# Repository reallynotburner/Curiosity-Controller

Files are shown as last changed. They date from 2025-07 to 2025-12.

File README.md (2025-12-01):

# Curiosity-Rover

<p style="text-align: center;">
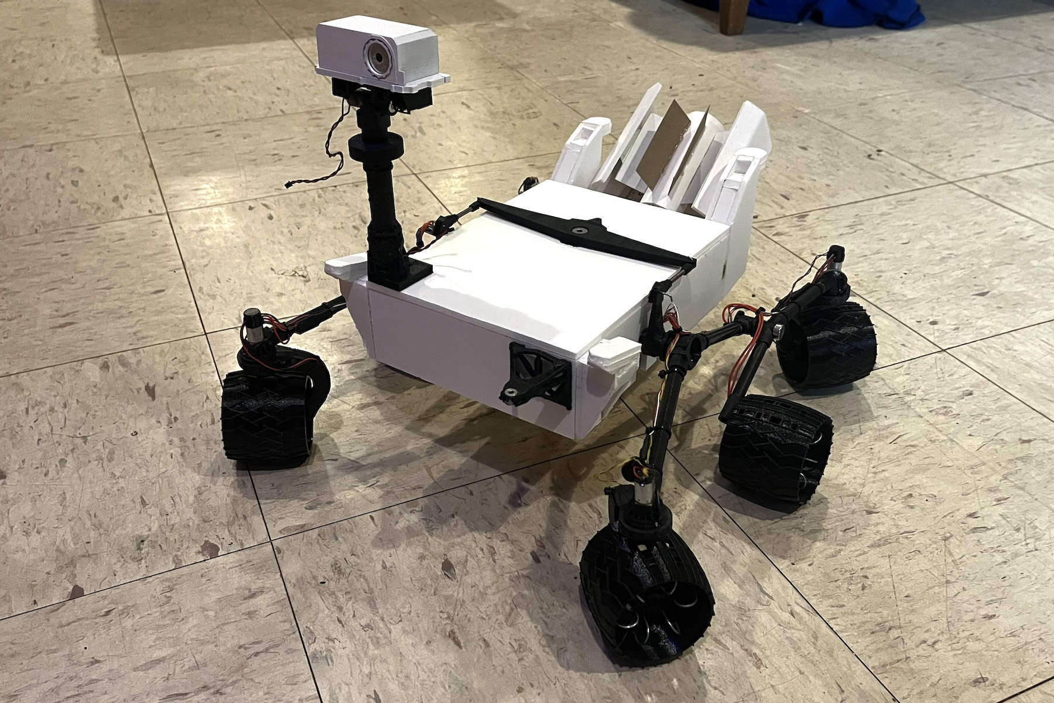
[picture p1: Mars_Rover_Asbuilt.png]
    
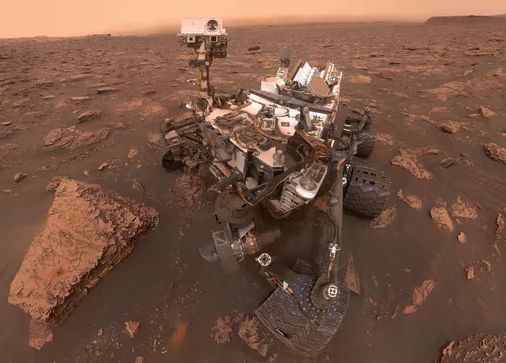
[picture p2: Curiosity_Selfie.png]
    
</p>

## Goal
###
I want to drive around a highly functional model of the Mars Science Laboratory (MSL), named [Curiosity](https://www.jpl.nasa.gov/missions/mars-science-laboratory-curiosity-rover-msl/).  It will have working rocker-bogie suspension, and 4 steerable motors so it can spin in place without skid steering like a tank.  I'm making it as small as I can using [Sanyo-style micro gearmotors](https://www.amazon.com/gp/aw/d/B07FVMVGM3/?_encoding=UTF8), which are inexpensive, strong, and fairly small.  The motors have to fit inside the wheel hubs and the steering mechanism without altering the proportions of the model too much for my taste.  Therefore the smallest I can make it is 1/6 scale, I could go smaller but it would mean more expensive smaller motors.

## Wiring
###
Using [Fritzing](https://fritzing.org/), a companion project of the [Arduino](https://www.arduino.cc/) movement, to document the physical orientation of all the wires that I'm putting in this thing.  You can draw wires, place components in solderless breadboards, all visually and intuitively while you make real connections on your project.  It generates schematics and node trees that can be used to order real PCB's to build the project more permanently.

<p style="text-align: center;">
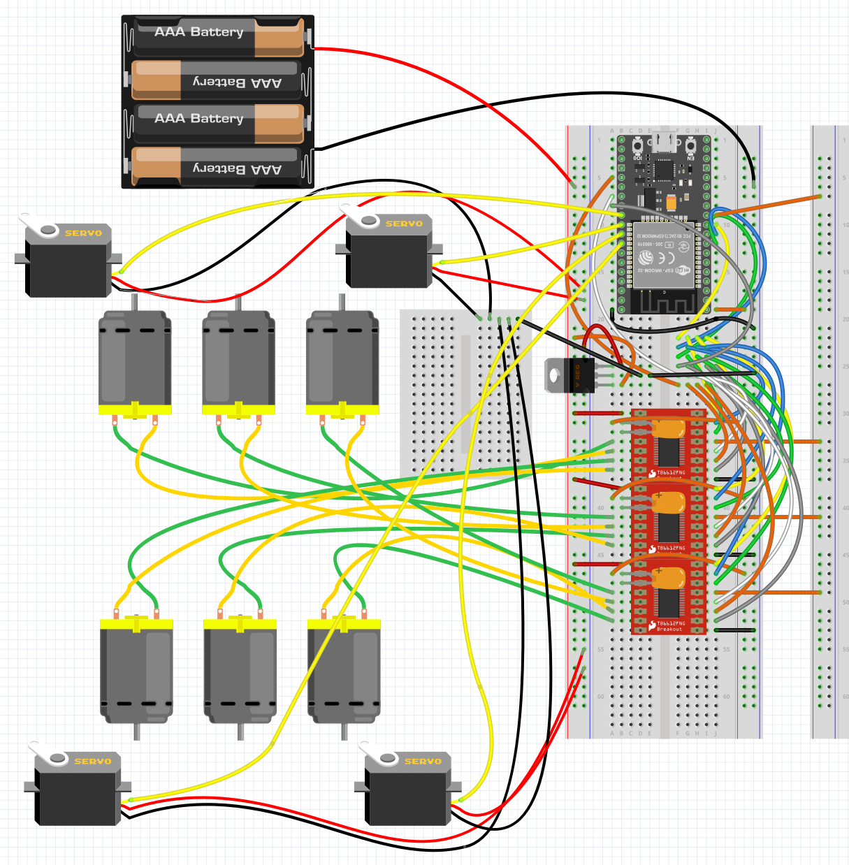
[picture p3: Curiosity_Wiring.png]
    
</p>

## Hardware
### Controller
[ESP32 Devkit](https://www.microcenter.com/product/613822/inland-esp32-wroom-32d-module) as a central controller has many input-output pins, nearly all of which can do motor controlling functions like PWM.  This is vital when it needs 10 independent motors just to drive around.  The ESP32 also has WiFi and Bluetooth built in, providing an inexpensive method of remote control.
### Interface
Uses standard web page interface, served via access point protocol. Open your phone, tablet or desktop computer and log into "curiosity".  The password is "marsrover".  Then open a browser to "controller.local" and the control UI will show up, allowing you to control the rover.

### Motors
[Sanyo-style micro gearmotors](https://www.amazon.com/gp/aw/d/B07FVMVGM3/?_encoding=UTF8) provide the traction and steering functions of the model.  They may even provide animation of the [Mast Camera](https://science.nasa.gov/mission/msl-curiosity/science-instruments/#h-mastcam) and Robotic Arm, but that is a project more complex than just driving the model around.

### Motor Driver
[DRV8833 H-Bridges](https://www.amazon.com/VKLSVAN-DRV8833-h-Bridge-Arduino-Microcontroller/dp/B0DQGQ1V1C) provide control of 2 motors per module, so there will be 3 of these on the model for driving.

### 10k Potentiometers
[Potentiometers](https://www.amazon.com/Taiss-Potentiometer-Variable-Resistors-Terminals/dp/B09XDR799P) are often used as volume controls.  I'm using them as a position sensor for the steerable wheels.  They convert an angle of the steering bracket into a voltage, which can be a feedback signal for standard hobby servo motor PCB's.

### Code Acknowledgements
- [Arduino platform](https://www.arduino.cc/) for their wonderful hardware & programming environment, start here if you want to build anything but don't know how to do any of it.
- [Fritzing GmbH](https://fritzing.org/) for their wiring schematic and PCB generation platform.
- [ESPRESSIF](https://www.espressif.com/en/producttype/esp32-wroom-32) a Chinese organization known for their superb wireless hardware, with software examples that are easily used in Arduino or standalone.
- [ARM Limited, et al.](https://github.com/littlefs-project/littlefs) simplifies putting the resources for the web app on the ESP32.
- [me-no-dev and Lacamera](https://github.com/lacamera/ESPAsyncWebServer) for their ESP WebServer, making it a trivial task to have a web browser serve your web application.
- [Rui Santos & Sara Santos Random Nerd Tutorials](https://RandomNerdTutorials.com/esp32-websocket-server-sensor/) for their websocket demo for ESP32 and Web, enabling real-time control from the app to the rover.
- [Yoann Moinet](https://github.com/yoannmoinet/nipplejs) for his ephemeral and intuitive joystick library "NippleJS".
- [Kevin Harrington and John K. Bennet](https://madhephaestus.github.io/ESP32Servo/annotated.html) for their ESP32 compatible PWM library, I couldn't make the default Espressif implementation work.
- [Benoit Blanchon](https://arduinojson.org/?utm_source=meta&utm_medium=library.properties) for his ArduinoJson library, making the two-way communication protocal simple, and transferrable across web, wifi and http.

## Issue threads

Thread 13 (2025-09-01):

Calibration Feature is broken

reallynotburner, 2025-09-01:
The ability to adjust and store the values of the custom center positions has failed, not sure which commit broke it.

reallynotburner, 2025-09-06:
Resolved with pull https://github.com/reallynotburner/Curiosity-Controller/pull/17

Closed 2025-09-06.

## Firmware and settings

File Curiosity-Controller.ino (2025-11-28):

/*********
  Curiosity Controller
  Drivable scale model of the Mars Science Laboratory, AKA, "Curiosity"
  Based on code examples by:
  Rui Santos & Sara Santos - Random Nerd Tutorials: 
  https://RandomNerdTutorials.com/esp32-websocket-server-sensor/
  Frank Poth:
  https://github.com/pothonprogramming/pothonprogramming.github.io/tree/master/content/touch-controller
  pcbreflux:
  https://github.com/pcbreflux/espressif/tree/master/esp32/arduino/sketchbook/ESP32_APA102

  reallynotburner@gmail.com
  Joshua Brown 2025 

  Permission is hereby granted, free of charge, to any person obtaining a copy of this software and associated documentation files.
  The above copyright notice and this permission notice shall be included in all copies or substantial portions of the Software.
*********/
#include <Arduino.h>
#include <WiFi.h>
#include <AsyncTCP.h>
#include <ESPAsyncWebServer.h>
#include "LittleFS.h"
#include <ArduinoJson.h>
#include <ESPmDNS.h>
#include <ESP32Servo.h>
#include <curiosity-defs.h>
#include <led-array.h>

// Create AsyncWebServer object on port 80
AsyncWebServer server(80);

// Create a WebSocket object
AsyncWebSocket ws("/ws");

bool calibrating = false;
bool isSpinning = false;
unsigned short calibrationAxis = 0;

void notifyClients(String sensorReadings) {
  ws.textAll(sensorReadings);
}

void steer (float horizontal) {
  // find steering values
  int diff = 0;
  int outerDiff = 0;
  int value01 = 0;
  int value02 = 0;
  int value05 = 0;
  int value06 = 0;
  if (!calibrationAxis) {  // regular steering, control all motors
    diff = (int)(500.0 * horizontal);
    // do some trig.
    // sin() is in radians.  horizontal = 0 is pointing straight ahead.
    // horizontal = 1 is about 2 radians so...
    outerDiff = (int)(diff / 2);

    if (diff > 0) {
      value01 = steerCal01 - outerDiff + 1500;
      value02 = steerCal02 + diff + 1500;
      value05 = steerCal05 + outerDiff + 1500;
      value06 = steerCal06 + diff + 1500;
    } else {
      value01 = steerCal01 - diff + 1500;
      value02 = steerCal02 + outerDiff + 1500;
      value05 = steerCal05 + diff + 1500;
      value06 = steerCal06 + outerDiff + 1500;
    }
    steer01.writeMicroseconds(value01);
    steer02.writeMicroseconds(value02);
    steer05.writeMicroseconds(value05);
    steer06.writeMicroseconds(value06);
  } else {  // calibration mode, only do one motor at a time
    diff = (int)(50.0 * horizontal);
    switch (calibrationAxis) {
      case 0:  // no axes are being calibrated
        break;
      case 1:  // calibrate steering servo 1
        value01 = diff + steerCal01 + 1500;
        steer01.writeMicroseconds(value01);
        if (!calibrating) {  // hopefully only happens infrequently
          steerCal01 = steerCal01 + diff;
          storeValue(steerKey01, steerCal01);
        }
        break;
      case 2:  // calibrate steering servo 2
        value02 = diff + steerCal02 + 1500;
        steer02.writeMicroseconds(value02);
        if (!calibrating) {  // hopefully only happens infrequently
          steerCal02 = steerCal02 + diff;
          storeValue(steerKey02, steerCal02);
        }
        break;
      case 5:  // calibrate steering servo 5
        value05 = diff + steerCal05 + 1500;
        steer05.writeMicroseconds(value05);
        if (!calibrating) {  // hopefully only happens infrequently
          steerCal05 = steerCal05 + diff;
          storeValue(steerKey05, steerCal05);
        }
        break;
      case 6:  // calibrate steering servo 6
        value06 = diff + steerCal06 + 1500;
        steer06.writeMicroseconds(value06);
        if (!calibrating) {  // hopefully only happens infrequently
          steerCal06 = steerCal06 + diff;
          storeValue(steerKey06, steerCal06);
        }
        break;
      default:
        break;
    }
  }
}

void updateMotors(String message) {
  float mappedVertical = 0;
  float mappedHorizontal = 0;

  JsonDocument messageObject;
  deserializeJson(messageObject, message);

  float horizontal = messageObject["horizontal"];
  float vertical = messageObject["vertical"];
  calibrationAxis = messageObject["calibrationAxis"];
  calibrating = messageObject["calibrating"];
  isSpinning = messageObject["spin"];
  if (isSpinning) {
    spin(horizontal);
  } else if (vertical > 0.0 && !calibrationAxis) {
    steer(horizontal);
    forward(vertical, horizontal);
  } else if (vertical < 0.0 && !calibrationAxis) {
    steer(horizontal);
    backward(vertical, horizontal);
  } else { // calibration mode, 
    steer(horizontal);
    stop();
  }
}

void handleWebSocketMessage(void *arg, uint8_t *data, size_t len) {
  AwsFrameInfo *info = (AwsFrameInfo *)arg;
  if (info->final && info->index == 0 && info->len == len && info->opcode == WS_TEXT) {
    // How to ingest the incoming data from web clients, without weird symbols and overflow values:
    String rawData = (char *)data;
    String message = rawData.substring(0, len);
    updateMotors(message);
    String sensorReadings = getSensorReadings();
    notifyClients(sensorReadings);
  }
}

void onEvent(AsyncWebSocket *server, AsyncWebSocketClient *client, AwsEventType type, void *arg, uint8_t *data, size_t len) {
  switch (type) {
    case WS_EVT_CONNECT:
      Serial.printf("WebSocket client #%u connected from %s\n", client->id(), client->remoteIP().toString().c_str());
      ledCautionAlert();
      break;
    case WS_EVT_DISCONNECT:
      Serial.printf("WebSocket client #%u disconnected\n", client->id());
      stop();
      ledCriticalAlert();
      break;
    case WS_EVT_DATA:
      handleWebSocketMessage(arg, data, len);
      ledReceiveAlert();
      break;
    case WS_EVT_PONG:
    case WS_EVT_ERROR:
      break;
  }
}

void initWebSocket() {
  ws.onEvent(onEvent);
  server.addHandler(&ws);
}

void setup() {
  Serial.begin(115200);

  WiFi.softAP(ssid, password);

  initLittleFS();
  initWebSocket();

  // Web Server Root URL
  server.on("/", HTTP_GET, [](AsyncWebServerRequest *request) {
    request->send(LittleFS, "/index.html", "text/html");
    blueOn();
    delay(200);
    allLedsOff();
  });
  server.serveStatic("/", LittleFS, "/");
  server.begin();

  if (!MDNS.begin("controller")) { // app is at http://controller.local
    Serial.println("Error setting up mDNS");
    while (1) {
      delay(1000);
    }
  }
  Serial.println("mDNS responder started");

  initMotor();
  initSteering();
  initLedArray();
  greenOn();
  delay(500);
  allLedsOff();
}

void loop() {
  if ((millis() - lastTime) > timerDelay) {
    String sensorReadings = getSensorReadings();
    notifyClients(sensorReadings);
    lastTime = millis();
  }
  ws.cleanupClients();
}

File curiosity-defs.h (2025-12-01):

#ifndef CURIOSITY_HEADER // Replace MY_HEADER_H with a unique identifier, usually based on the filename
#define CURIOSITY_HEADER

#include <ArduinoJson.h>
#include <Preferences.h>

// Store preferences, like steering calibration
Preferences preferences;

// Replace with your network credentials
const char *ssid = "curiosity";
const char *password = "marsrover";

// Motor Driver pins
const int PWM01 = 26;
const int AN1 = 33;
const int AN2 = 25;
const int STBY = 27;
const int PWM02 = 16;
const int BN1 = 4;
const int BN2 = 2;

// setting motor PWM properties
const int freq = 5000;
const int resolution = 8;

// steering pins
const int STEER01 = 19;
const int STEER02 = 17;
const int STEER05 = 18;
const int STEER06 = 5;
Servo steer01;
Servo steer02;
Servo steer05;
Servo steer06;

// uS +/- of center to add to the incoming controls
short steerCal01 = 0;          // calibration from preferences
short steerCal02 = 0;
short steerCal05 = 0;
short steerCal06 = 0;
char *steerKey01 = "steer01";  // the name of the calibration value for storage and retrieval
char *steerKey02 = "steer02";
char *steerKey05 = "steer05";
char *steerKey06 = "steer06";

// Timer variables
unsigned long lastTime = 0;
unsigned long timerDelay = 10000;

// 182.65 reading units per volt.
// 5.20 volts as 5.193 volts 
const int supplySense = 32;
float voltageRatio = 182.7;

float getVoltage(int pin) {
  int voltageValue = analogReadMilliVolts(pin);
  float voltageConverted = voltageValue / voltageRatio;
  // Serial.print("Voltage Sensed: ");
  // Serial.print(voltageConverted);
  // Serial.println(" volts");
  return voltageConverted;
}

void initMotor() {
  // configure motor PWM
  pinMode(PWM01, OUTPUT);
  pinMode(PWM02, OUTPUT);

  // set the control pins as outputs
  pinMode(AN1, OUTPUT);
  pinMode(AN2, OUTPUT);
  pinMode(BN1, OUTPUT);
  pinMode(BN2, OUTPUT);
  pinMode(STBY, OUTPUT);

  digitalWrite(STBY, HIGH);
  digitalWrite(AN1, LOW);
  digitalWrite(AN2, LOW);
  digitalWrite(BN1, LOW);
  digitalWrite(BN2, LOW);
}

// Get Sensor Readings and return JSON object
String getSensorReadings() {
  JsonDocument sensorReadings;
  sensorReadings["temperature"] = "Hot!";
  sensorReadings["humidity"] = "Moist!";
  sensorReadings["pressure"] = "Vacuous!";
  float supplyVoltage = getVoltage(supplySense);
  sensorReadings["supplyVoltage"] = supplyVoltage;
  sensorReadings["cal01"] = steerCal01;
  sensorReadings["cal02"] = steerCal02;
  sensorReadings["cal05"] = steerCal05;
  sensorReadings["cal06"] = steerCal06;
  char serializedReadings[256];
  serializeJson(sensorReadings, serializedReadings);
  return serializedReadings;
}

// Initialize LittleFS
void initLittleFS() {
  if (!LittleFS.begin(true)) {
    Serial.println("An error has occurred while mounting LittleFS");
  }
  Serial.println("LittleFS mounted successfully");
}

void forward(float vertical, float horizontal) {
    unsigned int mappedVertical = (unsigned int) abs(vertical * 255.0);
    unsigned int mappedHorizontal = (unsigned int) abs(horizontal * 64.0);
    digitalWrite(AN1, HIGH);
    digitalWrite(AN2, LOW);
    digitalWrite(BN1, HIGH);
    digitalWrite(BN2, LOW);
    if (horizontal > 0) {
      analogWrite(PWM01, mappedVertical - mappedHorizontal);
      analogWrite(PWM02, mappedVertical);
    } else {
      analogWrite(PWM01, mappedVertical);
      analogWrite(PWM02, mappedVertical - mappedHorizontal);
    }
    // Serial.print("forward: ");
    // Serial.println(mappedVertical);
}

void backward(float vertical, float horizontal) {
    unsigned int mappedVertical = (unsigned int) abs(vertical * 255.0);
    unsigned int mappedHorizontal = (unsigned int) abs(horizontal * 64.0);
    digitalWrite(AN1, LOW);
    digitalWrite(AN2, HIGH);
    digitalWrite(BN1, LOW);
    digitalWrite(BN2, HIGH);
    if (horizontal > 0) {
      analogWrite(PWM01, mappedVertical - mappedHorizontal);
      analogWrite(PWM02, mappedVertical);
    } else {
      analogWrite(PWM01, mappedVertical);
      analogWrite(PWM02, mappedVertical - mappedHorizontal);
    }
    // Serial.print("backward: ");
    // Serial.println(mappedVertical);
}
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

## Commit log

2025-07-16 replaced web app with Frank Poth's demo
    [Curiosity-Controller.ino]
2025-07-18 added some remote buttons
2025-07-20 moved from button array to button object, don't remember why I wanted that though
2025-07-20 now can control motor with forward and backward button
2025-07-23 fixed non-linear motor speed control bug, adding Fritzing wiring diagram, in progress
    [Wiring.fzz]
2025-07-23 added filter caps to the Vcc-GND on each motor driver in Wiring
    [Wiring.fzz]
2025-07-23 udpated with some minor steering code - in progress
2025-07-26 added the wires to the first servo and first motor controller
    [Wiring.fzz]
2025-07-27 now stores data persistently across reboots, TODO: actually store usable data for each steerable wheel
    [Curiosity-Controller.ino]
2025-07-27 now have a working preference storage pattern, TODO: provide calibration method
2025-07-27 now with centered buttons and joystick controller
2025-07-31 sending calibration status from the web page, todo: receive the data
2025-08-03 now with working, persistent calibration mode
2025-08-13 added steering05 and steering 06
2025-08-24 added rest of steering servos, fixed missing break statements
    [Curiosity-Controller.ino, curiosity-defs.h]
2025-08-24 fixed white space changes to make PR look better
    [Curiosity-Controller.ino]
2025-08-24 added the right side motors
2025-08-24 documented wiring changes to Wiring schematic
    [Wiring.fzz]
2025-08-24 udpated Readme, updated Wiring schematic
    [Wiring.fzz]
2025-09-01 only have to fix the 02 steering during spin mode
    [Curiosity-Controller.ino, curiosity-defs.h]
2025-09-01 now spin and regular steering are working
2025-09-06 added supply voltage feedback
2025-09-06 fixed calibration mode
2025-09-18 updated calibrated value for Volts readout
2025-09-19 now with rudimentary display for calibration values
2025-09-19 hopefully adding connection from calibration values all the way out to the UI
2025-11-28 added status led, added cooldown timing to the client making requests to the controller
2025-11-28 fixed forward slalom motion, TODO: fix rear slalom
    [Curiosity-Controller.ino, curiosity-defs.h]
2025-11-28 fixing up some steering items
    [Curiosity-Controller.ino, curiosity-defs.h]
2025-12-01 fixed spin in opposite direction problem
    [curiosity-defs.h]
